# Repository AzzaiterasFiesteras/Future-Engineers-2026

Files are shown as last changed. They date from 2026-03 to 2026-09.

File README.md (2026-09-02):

<h1 align="center">Future Engineers 2026 </h1>

<table>
  <tr>
    <td>
      <p align="center">
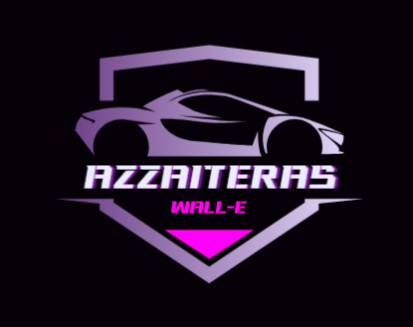
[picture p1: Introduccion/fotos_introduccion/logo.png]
Top View
      
  </tr>
</table>

 ### 📌 Table of Contents

> [!TIP]
> Click the arrow below 👇 to expand the **Table of Contents**.  
> Every item is a clickable link to a folder or README file in this repository.

<details>
<summary><b>📂 Table of Contents</b></summary>

1. [Summary README](/README.md)

2. [Introduction](/Introduccion/)  
   - [Objective](/Introduccion/Objetivo.md)
   - [Team presentation](/Introduccion/Presentacion_equipo.md)
  
3. [Initial Conditions](/Condiciones_Previas/Condiciones_Previas.md)
   -  [Materials and hardware - software relation](/Condiciones_Previas/Materiales_acabado.md)
     
4. [Mechanics](/Mecánica/)
   - [Chassis](/Mecánica/Chasis.md)
   - [Steering system](/Mecánica/Direccion.md)
     
5. [Electronics](/Electrónica/)
   - [Power system](/Electrónica/Alimentacion.md)
   - [Design](/Electrónica/Diseño.md)
   - [Components](/Electrónica/Componentes.md)
     - Servomotor
     - Board
     - Shield
     - Ultrasonic sensors
     - Gyroscope
     - Motor
     - Bateries
 6. [Programme](/Programación/)
    - [Programme development](/Programación/Explicacion_programa.md)
    - [Flow charts](/Programación/Pensamiento_lógico.md)
  7. [3D Files](/Archivos_en3D/)
  9. [Analysis](/Análisis/)
     - [Detected problems](/Análisis/Problemas_detectados.md)
     - [Improvement proposals](/Análisis/Propuestas_de_mejora.md))
   10. [Final results](/Resultado/)
11. [Conclusion](/Conclusiones/)
    - Acquired knowleadge
12. [Bibliography](/Bibliografía/)
    - Arduino
    - Tinkercad
    - PixyCam
    - LucidChart
</details>

##  Team Introduction & Team Information
<table>
  <tr>
    <td align="center" width="33%">
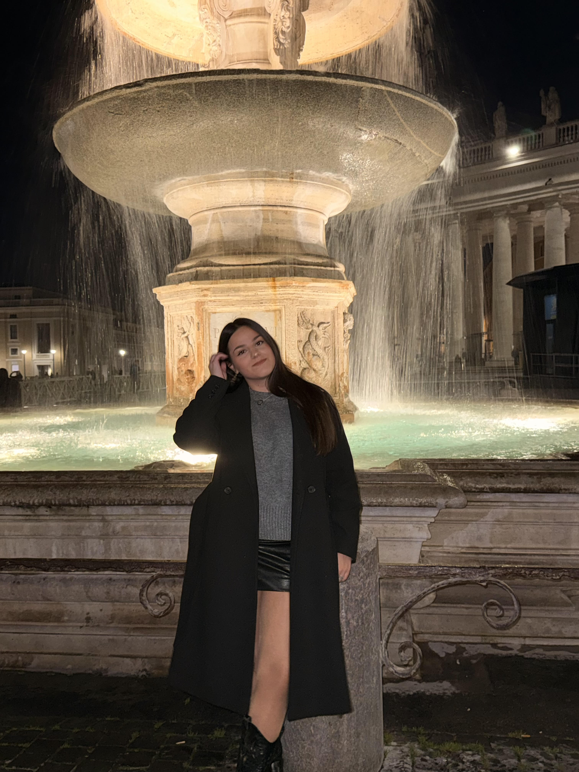
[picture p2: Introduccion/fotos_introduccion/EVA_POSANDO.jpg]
      <br>
      <strong>EVA ESPINOSA ORTIZ</strong><br>
      <em>Lead programmer</em><br>
      <sub>Sensor Integration, Logic, Obstacle Avoidance</sub>
    </td>
    <td align="center" width="33%">
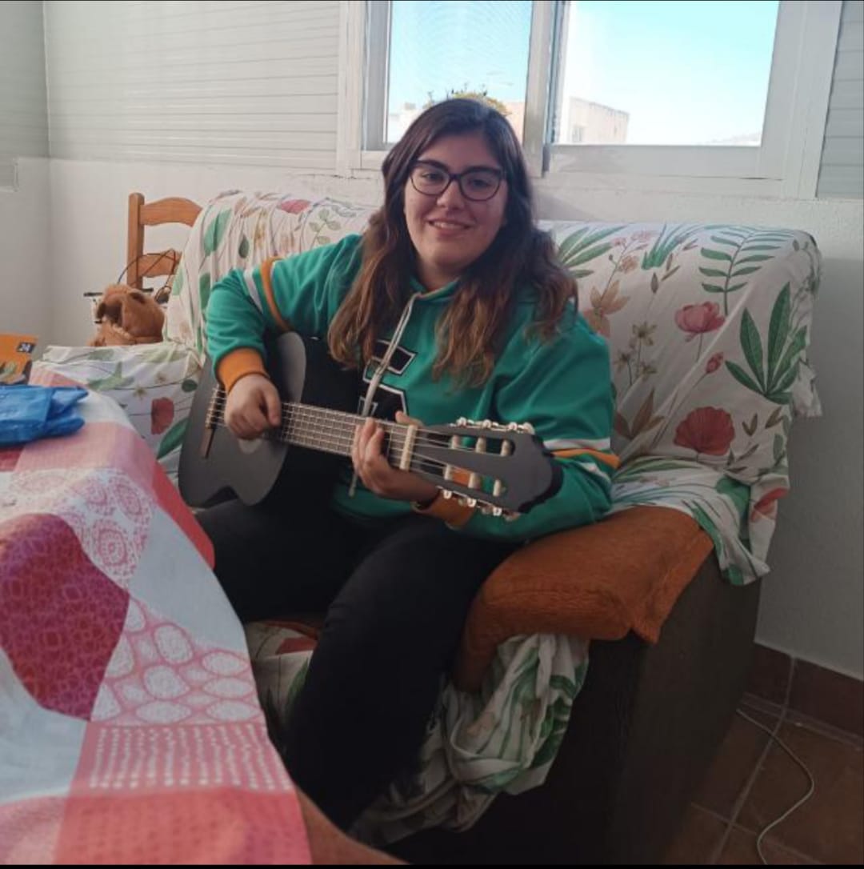
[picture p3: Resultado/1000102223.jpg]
      <br>
      <strong>LIDIA REQUENA TORRES</strong><br>
      <em>Hardware Engineer</em><br>
      <sub>Wiring, Circuit Design, Power Management</sub>
    </td>
    <td align="center" width="33%">
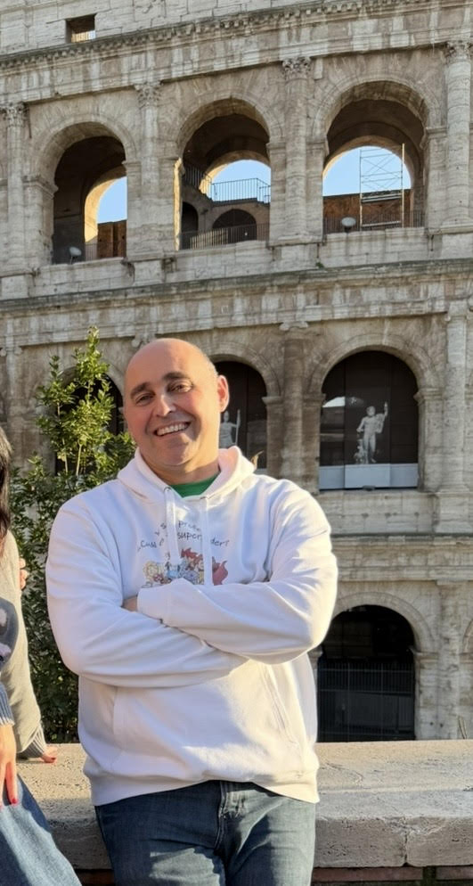
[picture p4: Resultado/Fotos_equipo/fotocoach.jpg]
      <br>
      <strong>ANTONIO MUÑOZ PANCORBO</strong><br>
      <em> Coach</em><br>
      <sub>Support and guidance </sub>
    </td>
  </tr>
</table>

---

## Introduction 
> [!WARNING]
> Click the link below 👇 to see more information about the introduction.
> 
> [For more information click here](Introduccion/)

> [!IMPORTANT]
> Click the link below 👇 to see the final result of our robot.

(https://www.youtube.com/watch?v=cXj32blsBB0)

### Presentation 
Our team´s robot is called WALLE. WALLE was designed for the Future Engineers challenge of the World Robot Olympiad. In this challenge we must complete 2 rounds. The first one, called Open Challenge, consists of completing 3 full laps around a board whose internal walls are placed randomly. The second, called Obstacle Challenge, also requires three laps on a board changing, but with the added difficulty of avoiding obstacles. Depending on the obstacles´colors (red or green) it must be avoided from the right side or the left side.
> [!WARNING]
> Click the link below 👇 to see more information.
> 
> [For more information click here](Introduccion/Objetivo.md)

### Initial Conditions
To properly carry out this project, this robot has been previously designed according to some specific rules and conditions. We had complete freedom to use any material, such as plastic, wood or even Lego pieces. However, we had a limitation in the robot´s size. The robot can not exceed 30cm x 30cm. We adapted its design in all these conditions, with special care in the front steering gear, since it was not allow to make turns with the independent motors´control as they had to be conected in the same pin. This force us to design a front steering gear with a servomotor.
> [!WARNING]
> Click the link below 👇 to see more information.
> 
> [For more information click here](Condiciones_Previas/Condiciones_Previas.md)

## Materials and hardware - software relation
1. `3D printed chassis and pins`: allows the placement of all the components with the enough space for the front steering gear not to interference with the rest of the components.
2. `Arduino Uno board`: controls all the robot´s components, such as the motors, the servomotor or the sensors. These are connected to the Arduino board
3. `MG996R servo motor`:  main responsible for the front steering gear. This is controlled by a servos library in the Arduino Ide program.
4. `TT model motor with 1:40 speed reduction`: provide robot movement. These are connected to the L298N motor driver shield for control.
5. `Wheels with a diameter of [cm]`: connected to the rear motors for their control.
6. `Three HC-SR04 ultrasonic sensors for measuring distances`: must measure and calculate the distance between the walls and the obstacles.
7. `Electronic wiring: breadboard, male-to-male jumper wires, female-to-male jumper wires, and L298N shield for motor control`: wires, protoboard and motor driver shield. Allows the comunication between the Arduino board and the rest of the components.
 8.   `Power supply`: two 3.7V 9900mAh 18650 batteries connected in series within their battery holder that provide enough energy for the correct running of the robot.
10.` BNO055 gyroscope`: allows the robot to make turns much more precisely by setting itself to specific degrees at the program.
11. `Front wheel mechanism`: made by 3D printed pieces that hold the mechanism for the robot to make turns correctly.
> [!WARNING]
> Click the link below 👇 to see more information.
> 
> [For more information click here](Condiciones_Previas/Materiales_acabado.md)

## Mechanics 
### Chassis 
For the chassis design, we opted for a smaller one than in previous years to facilitate turns on the board We also addressed the lack of space for all the components by adding an upper level where we would place the circuit board, breadboard, shield, and later, the camera. However, we also had to adjust the design to accommodate a single rear motor for the robot's drive. Therefore, we drilled two holes in the lower level of the chassis (where the ultrasonic sensors, servo motor, and front wheel mechanism are located) for the wheels. We also maintained the front wheel design from previous years. We created a small protrusion to house the servo motor and all the necessary steering mechanism components. One of the three ultrasonic sensors, in this case, the center one, would also be located on this same protrusion.

> This forms the base of the robot, upon which the other platforms will be stacked using a series of pins screwed to the structure. These plates will be secured with screws and will serve as a support for the installation of the remaining necessary components.

> [!WARNING]
> Click the link below 👇 to see more information.
>  
> [For more information click here](Mecánica/Chasis.md)

### Steering system
The steering system created is composed by an amount of components designed in 3D which act as a support and it allows you to control the trajectory you decide to make, through turns, with the servo motor and the steering system. The steering system consists of two bars which are attached to articulated joints. The bar below is the guideline that is part of the servomotor shaft. This bar is connected to the bar below through an articulated joint, as aformentioned. When the bar from above move, it allows the steering system to guide the wheels. 
> [!WARNING]
> Click the link below 👇 to see more information.
> 
>[For more information click here](Mecánica/Direccion.md)

## Electronics
### Power system
One of the the major problems was being able to prove the necessary energy to all the components. o solve this, we used two rechargeable 18650 batteries of 9900 mAh each, connected in series to a battery holder. Other options, such as AAA batteries in series, 9V batteries, or even rechargeable 9V batteries of 1300 mAh, were not efficient enough and caused voltage drops.
> [!WARNING]
> Click the link below 👇 to see more information.
> 
> [For more information click here](Electrónica/Alimentacion.md)

## Components

| Quantity | Status | Description |
| ---| --- | ---|
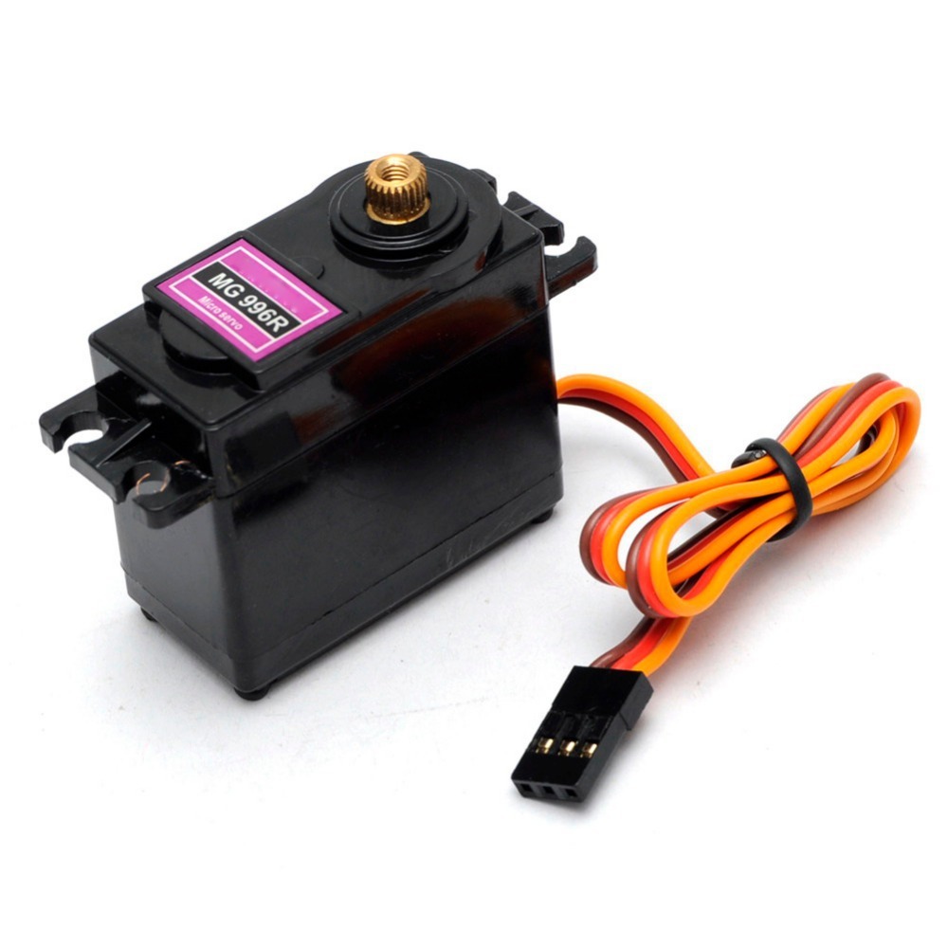
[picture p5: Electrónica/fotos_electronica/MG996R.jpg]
Servomotor MG996R
| 1 | Servomotor |  |
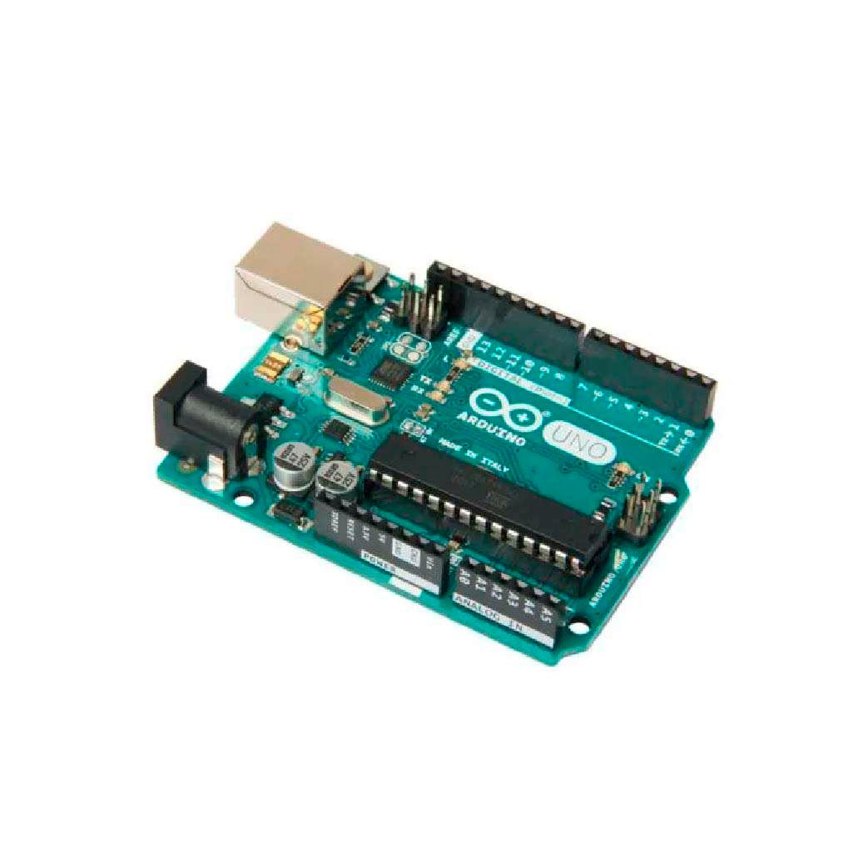
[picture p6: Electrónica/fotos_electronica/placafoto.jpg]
Arduino Uno R3 Board
| 1 | Board |  |
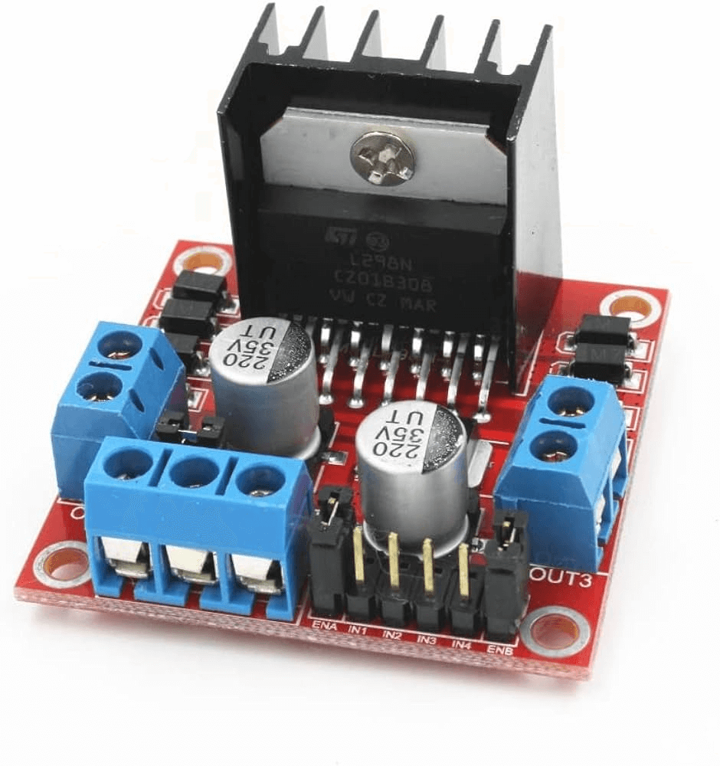
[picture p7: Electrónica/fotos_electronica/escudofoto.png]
Shield
| 1 |Shield |  |
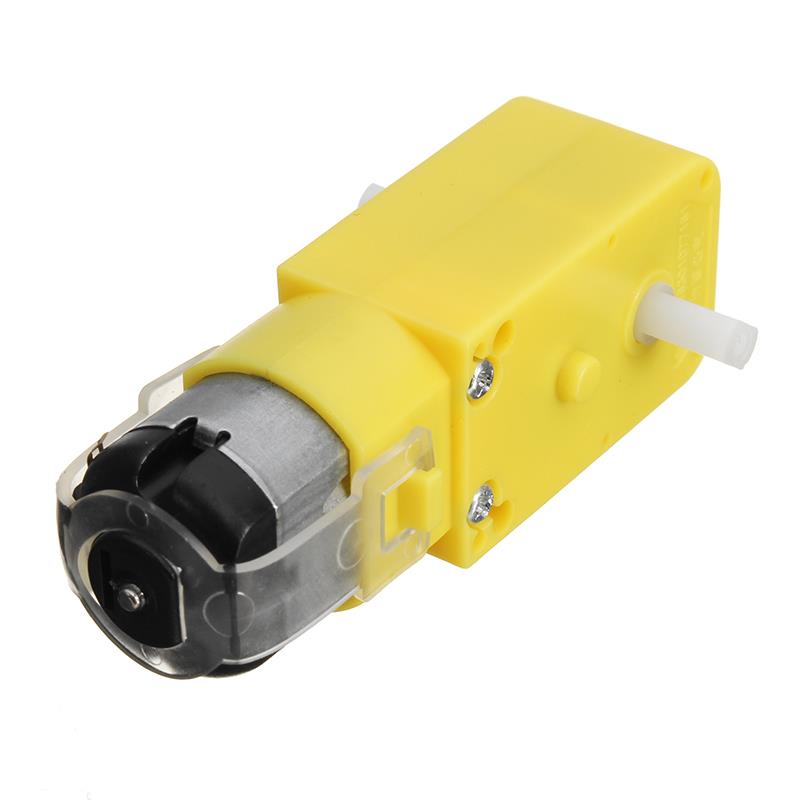
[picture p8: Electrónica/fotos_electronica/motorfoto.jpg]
Motor
| 1 |Motor|  |
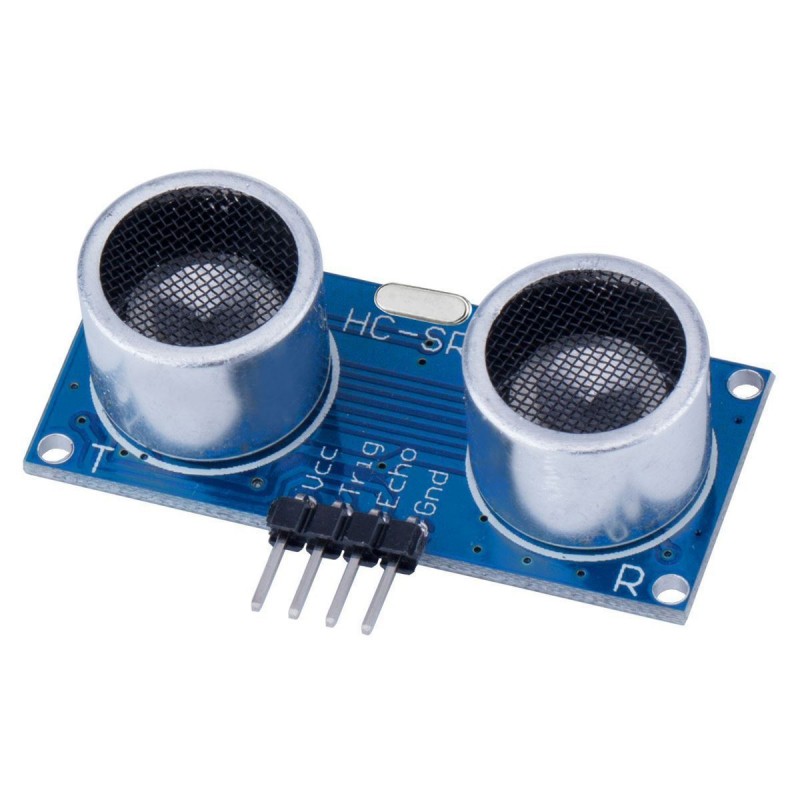
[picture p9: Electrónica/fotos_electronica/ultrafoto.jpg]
Ultrasonic sensor
| 3 | Ultrasonic sensors|  |
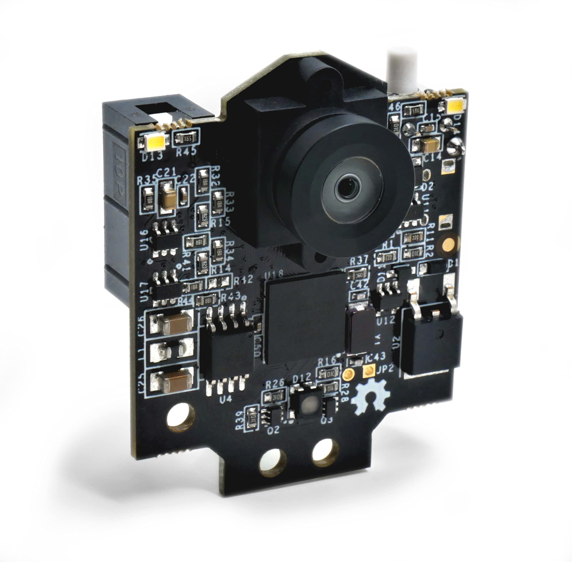
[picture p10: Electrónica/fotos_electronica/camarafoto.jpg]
Camera PixyMon 2
| 1 | Camera PixyMon 2 |  |
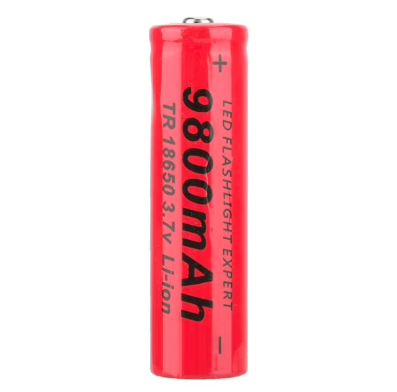
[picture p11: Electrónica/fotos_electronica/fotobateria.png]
Batteries
| 2 | Batteries |  |
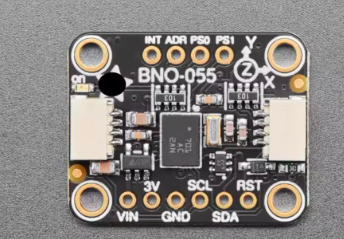
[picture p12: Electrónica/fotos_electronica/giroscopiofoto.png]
Gyroscope
| 1 | Gyroscope  |  |

### Servo Motor
For the front steering wheel was necessary the incorporation of a servo motor. We chose one that could make turns according to the turning angles to make it easier for us to program.

### Motors 
In order to WALLE to move, we used only two motors, which were installed in the back of our vehicle. To connect the motors, we used the L298N motor driver shield, which was used only as an output for controlling the motors.

### Motor driver shield
For the motor connections, we chose the L298N shield, because the previous shields were incompatible with the board. All we did was connect the shield's ena pin to pin 7 of the Arduino board to control the speed, and the motors to the in1 and in2 pins to turn them on and off.

### Sensors
To prevent the robot from crashing with walls, we used ultrasonic distance sensors. We also added a structure into the robot to hold the sensors. To program these, we created a distance measurer that allowed us to see the distance each sensor was measuring in real time on the serial monitor.

### Arduino board
We took the Arduino Uno board as we were already familiar with it. 

### Bateries
We used the 18650 batteries for our robot. Their maximum voltage is 4.2V, and the battery capacity is 9900mAh. These batteries are also rechargeable. We chose these over others due to the large number of components we had to power.

### Camera
In order to prevent the robot from crashing against obstacles, we used a PixyCam 2 Camera. This enables WALL-E to detect the color of the obstacle and decide which direction to turn (left if it is green or right if it is red).

### Gyroscope 
This component is mainly used to mesure the orientation and rotation of an object. It detects changes in angle of our robot. Henceforth, we decided to use it for its turns and for controlling the trajectory on the straight sections. We used the BNO055 gyroscope.

> [!WARNING]
> Click the link below 👇 to see more information.
> 
> [For more information click here](Electrónica/Componentes.md)

## Programme
### Open Challenge
``` c++
#include <Wire.h>
#include <Adafruit_Sensor.h>
#include <Adafruit_BNO055.h>
#include <Servo.h>
#include <Ultrasonic.h>

int ENA = 5;
int IN1 = 6;
int IN2 = 7;

Servo cochino;
Adafruit_BNO055 bno = Adafruit_BNO055(55);

const int pinservo = 9;
const int pinPulsador=13;

float anguloObjetivo;  
int centroServo = 35;  // Posición recta
int sentido = 0;       // 1 para derecha, 2 para izquierda
int contadorGiros = 0; // Control de esquinas para las 3 vueltas
int contador1=0;
int contador2=0;
bool start = false; 
```
Before developing the program logic, the first step was to install all the necessary libraries for controlling the different components of the robot, including the motors, the servo motor, the ultrasonic sensors, and the gyroscope, using #include <library_name>. The servo and the gyroscope were also declared and named, while the ultrasonic sensors were defined later in the code.

After that, all the main variables of the system were defined. The motor driver L298N pins were set (int ENA = 5, int IN1 = 6, int IN2 = 7) to control motor speed and direction. The servo motor pin was assigned (const int pinservo = 9). The variable float anguloObjetivo represents the target angle the robot must reach. int centroServo = 35 defines the position where the steering system is completely straight.

> In addition, int sentido = 0 is used to determine the initial turning direction (1 for right, 2 for left), starting at 0 until it is defined during execution. int contadorGiros = 0 is used to count the corners so the robot can stop after completing 3 laps (12 turns). The variables contador1 and contador2 are used to manage sensor-based detection conditions. Finally, bool start = false is a boolean variable that can only be true or false, initialized as false to keep the system off until it is activated by the push button.
``` C++
#define TRIG_IZQ 8
#define ECHO_IZQ 10
Ultrasonic ultraIZQ(TRIG_IZQ, ECHO_IZQ, 60000);
#define TRIG_CENTRO 3
#define ECHO_CENTRO 4
Ultrasonic ultraCENTRO(TRIG_CENTRO, ECHO_CENTRO, 60000);
#define TRIG_DERECH 11
#define ECHO_DERECH 12
Ultrasonic ultraDERECH(TRIG_DERECH, ECHO_DERECH, 60000);
```
> As we already know, ultrasonic sensors are made up of a trigger pin (which sends out a signal) and an echo pin (which receives the reflected signal). By measuring the time it takes for the signal to bounce back, we can calculate the distance to an object.
> To implement this in the program, we had to define which Arduino pins were connected to each trigger and echo pin of every sensor. The configuration was set as follows:
- Trigger (pin 8) and echo (pin 10) = left ultrasonic sensor
- Trigger (pin 3) and echo (pin 4) = center ultrasonic sensor
- Trigger (pin 11) and echo (pin 12) = right ultrasonic sensor
### Void setup
```C++
void setup() {
  Serial.begin(9600);
  pinMode(IN1, OUTPUT);
  pinMode(IN2, OUTPUT);
  pinMode(ENA, OUTPUT);
  pinMode(pinPulsador, INPUT_PULLUP);

  cochino.attach(pinservo);
  cochino.write(centroServo);
  
  Serial.println("Hola, iniciando sistema...");

  if (!bno.begin()) {
    Serial.println("No se encuentra el sensor BNO");
    while (1); // Bloqueo si no hay sensor
  }
  prepararSensor(); 
}
```
> The void setup() function is created at the beginning of the program and is executed only once when the system starts. Its main purpose is to initialize all the components required for the robot to operate correctly.
In our case, the serial port is activated to allow monitoring and calibration of sensor readings through the Serial Monitor. The servo motor pin is also configured so the steering system can start working from the beginning. In addition, the motors and the push button are initialized.A conditional statement is included to check whether the gyroscope is detected. If the BNO055 sensor is not found, an error message is printed in the serial monitor and the system is blocked to prevent further execution.
Finally, the gyroscope calibration function is called so the robot can determine its initial reference direction, often referred to as “north.”

### Void loop 
``` C++
 if (digitalRead(pinPulsador) == LOW) {
    start = true;
    Serial.print(2);
  }
  if (start == true) {
  // Lógica de fin de carrera: tras 12 giros (3 vueltas), el robot para
    if (contadorGiros >= 12) {
      terminarCarrera();
      while(1); 
    }
    int cmCentro = ultraCENTRO.Ranging(CM);
    float anguloAhora = obtenerGrados();
    int cmIzq = ultraIZQ.Ranging(CM);
    int cmDer = ultraDERECH.Ranging(CM);
```
> In the first part of the void loop, we programmed the push button so that when it is pressed, the whole program starts running. At the same time, it prints the number “2” in the Serial Monitor to verify that the button is working correctly. We also added the final race logic: after 12 turns (which equals three complete laps), the robot stops. After this, the program reads the sensor data and stores it in variables for later use. First, it measures the distances from the three ultrasonic sensors, meaning each sensor returns a value in centimeters. Then, the variable anguloAhora stores the result of the obtenerGrados() function, which returns the robot’s current orientation angle. This value is stored as a float because it can include decimal values.
``` C++
  if (cmCentro < 80) {
      contador1++;
    } else {
      contador1=0;
    }
    if (cmCentro < 140 && abs(cmIzq-cmDer)>120) {
      contador2++;
    } else {
      contador2=0;
    }
if (contador1>2 || contador2>2) {
      contador1=0;
      contador2=0;
      digitalWrite(IN1, LOW);
      digitalWrite(IN2, LOW);
      analogWrite(ENA, 0);
      delay(500);
```
> In these functions, the program uses two counters to detect when the robot needs to turn. First, the robot continuously checks the distances measured by its sensors. If it detects that it is getting too close to walls several times in a row, or if it detects an unusual situation where there is a large difference between the left and right sensor readings, it starts increasing these counters. These counters are used to make sure the situation is not just a random or temporary reading, but something that persists over time. In other words, it is a way to confirm that the sensor data is reliable. Basically, the robot does not react to a single measurement. Instead, it waits until the problem is repeated several times, and only then it responds by stopping to avoid crashing or continuing in an unsafe situation.
```C++
     if (contadorGiros == 0) {
        if (cmIzq < cmDer) sentido = 1; 
        else sentido = 2;              
        Serial.print("Sentido del circuito: ");
        Serial.println(sentido);
      }
      if (sentido == 1) hacerGiro(90);
      else hacerGiro(-90);

      contadorGiros++; 
      Serial.print("Esquina número: ");
      Serial.println(contadorGiros);
    }
```
>  It is at this point, when the robot reaches the first wall, that it decides whether the circuit will be followed on the left or on the right side. To do this, the program compares the distances measured on both sides. If the left distance is smaller than the right one, the variable sentido is set to 1, which corresponds to turning right. Otherwise, sentido is set to 2, which corresponds to turning left. Based on this decision, the robot executes the turn: if sentido is 1, it performs a 90-degree turn to the right, and if it is 2, it performs a -90-degree turn to the left.
At the same time, each turn is counted using a counter, since this value will later be used to stop the robot after completing the required number of laps. To verify that the system is working correctly, the current number of corners (and therefore turns) is displayed in the Serial Monitor.

```C++
else {
      digitalWrite(IN1, LOW);
      digitalWrite(IN2, HIGH);
      analogWrite(ENA, 200);

      // Ajuste de dirección para ir siempre rectos
      float diferencia = anguloObjetivo - anguloAhora;
      if (diferencia > 180) diferencia -= 360;
      if (diferencia < -180) diferencia += 360;

      // Si nos desviamos, el servo corrige automáticamente
      if (diferencia > 3) {
        cochino.write(centroServo + 12);
      } else if (diferencia < -3) {
        cochino.write(centroServo - 12);
      } else {
        cochino.write(centroServo);
      }
    } 
  }
}
```
> However, if the robot does not detect any walls, it means that the path is clear. In this case, the motors are activated and the speed is increased. At the same time, the direction is continuously adjusted to ensure the robot moves in a straight line. If the robot deviates from the correct path, the servo automatically corrects the steering to bring it back to a straight trajectory.

### Obstacle Challenge

## Code functions
| Function | Type | What does it do? | Use in the program |
| --- | --- | --- | --- |
| **`setup()`** | `void` | Initializes the entire robot system | Configures pins, starts serial communication, connects the servo, initializes the BNO055 sensor, and calibrates the gyroscope before starting |
| **`loop()`** | `void` | Continuously runs the robot’s main logic | Reads sensors, detects obstacles, controls movement, corrects direction, performs turns, and counts laps |
| **`obtenerGrados()`** | `float` | Gets the robot’s current angle | Reads the orientation from the BNO055 sensor and returns the current heading angle |
| **`prepararSensor()`**  | `void` | Calibrates the gyroscope | Waits until the sensor reaches maximum precision and stores the robot’s initial direction |
| **`hacerGiro()`** | `void` | Performs a controlled turn | Uses the servo and gyroscope to rotate the robot accurately |
| **`terminarCarrera()`** | `void` | Ends the race | Moves the robot forward for a few more seconds, stops the motor, and finishes execution |
| **`Serial.begin()`** | `void` | Starts serial communication | Allows messages to be sent to the Serial Monitor |
| **`Serial.print()`** | `void` | Prints information without a newline | Used for debugging and status messages |
| **`Serial.println()`**  | `void` | Prints information with a newline | Makes messages easier to read in the Serial Monitor |
| **`pinMode()`** | `void` | Configures a pin | Defines whether a pin is used as input or output |
| **`digitalWrite()`** | `void` | Turns a digital pin on or off | Controls motor direction and other devices |
| **`digitalRead()`** | `int` | Reads a digital pin | Detects whether the push button is pressed |
| **`analogWrite()`** | `void` | Sends a PWM signal | Controls motor speed |
| **`delay()`** | `void` | Pauses the program | Waits before continuing execution |
| **`abs()`** | `int / float` | Returns the absolute value | Used to calculate unsigned differences |
| **`attach()`** | `void` | Connects the servo | Enables Arduino to control the servo |
| **`write()`** | `void` | Moves the servo | Changes the steering direction |
| **`begin()`** | `bool` | Initializes the BNO055 sensor | Checks whether the sensor is working correctly |
| **`getEvent()`** | `void` | Retrieves sensor data | Reads orientation and motion data |
| **`getCalibration()`**  | `void` | Checks calibration level | Verifies gyroscope precision |
| **`Ranging()`** | `int` | Measures distance | Returns the distance detected by the ultrasonic sensor 

> [!WARNING]
> Click the link below 👇 to see more information.
> 
> [For more information click here](Programación/Explicacion_programa.md)                                                                                   |

## Compilation process
For programming, we use the Arduino IDE program. Once the program is complete, all we have to do is upload it to the board. The process of uploading the board is very simple; we just connect the board to the computer using a wire and download the program. This way, the robot is ready to work.

## Final results 
> [!WARNING]
> For seeing all the final products and our final result in the Open challenge, click the link below 👇 for seeing all the information with details.
> 
> [For more information click here](Resultado/Resultado_final.md)

## Conclusion and Analysis

> [!WARNING]
> For more information about all the acquired knowleadge and detected problems, click the link below  👇 for seeing all the information with details.
> 
> [For more information about detected problems click here](Análisis/Problemas_detectados.md)
> 
> [For more information about improvement proposals click here](Análisis/Propuestas_de_mejora.md)
> 
> [For more information about the conclusion and the acquired knowleadge click here](Conclusiones/Conocimientos_adquiridos.md)

## Bibliography 

<p align="left"> <a href="https://www.arduino.cc/" target="_blank" rel="noreferrer"> arduino </a> <a href="https://www.w3schools.com/cpp/" target="_blank" rel="noreferrer"> cplusplus </a> <a href="https://git-scm.com/" target="_blank" rel="noreferrer"> git </a> </p>

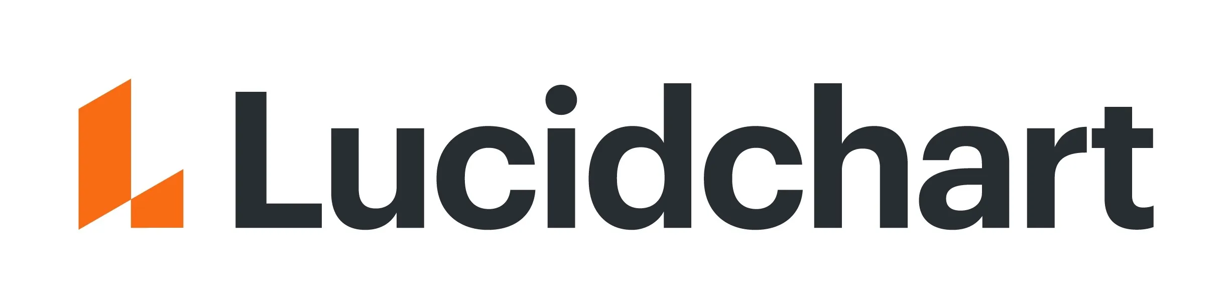
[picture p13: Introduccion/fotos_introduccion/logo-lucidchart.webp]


<p align="right">
  <a href="#top">
    
  </a>
</p>

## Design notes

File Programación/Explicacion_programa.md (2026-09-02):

# Funciones del código 

| **Funciones** |  **Sintaxis** | **Uso explicado** | 
| :--- | :---: | ---:|
| `setup()`|`void setup()`  |Se ejecuta una sola vez al encender la placa. Inicializa comunicación del puerto serie, configura pines, conecta el servo, inicia el sensor BNO055 y calibra el giroscopio| 
| `loop()`|`void loop()`  |Se ejecuta continuamente. Lee sensores ultrasónicos, detecta obstáculos, controla el movimiento, corrige dirección y cuenta los giros para completar las vueltas.| 
| `obtenerGrados()`|`float obtenerGrados() ` |Lee la orientación del sensor BNO055 y devuelve el ángulo en grados respecto al eje X `(orientation.x)`. Se usa para saber hacia dónde apunta el robot.| 
| `prepararSensor()`|`void prepararSensor() ` |Espera hasta que el giroscopio tenga máxima precisión `(gyro == 3)`. Después guarda el ángulo inicial como referencia en `anguloObjetivo.`| 
| `hacerGiro()`|`void hacerGiro(int grados) ` |Ajusta el objetivo angular y mueve el servo para girar el coche. El robot sigue girando hasta que el error sea menor a 5°.| 
| `terminarCarrera()`|`void terminarCarrera() ` |Hace que el coche avance un poco más para no seguir girando 8para que no llegue a chocarse con la pared interna) y luego apaga el motor.| 

## Funciones dentro del `void setup`

| **Funciones** | **Uso explicado** | 
| :--- | ---: |
| `Serial.begin(9600)`| Inicia comunicación del puerto serie. |
| `pinMode()`| Configura pines como entrada o salida |
| `cochino.attach(pinservo)`| Conecta el servo |
| `cochino.write(centroServo)`|`Coloca el servo centrado ` |
| `bno.begin()`|Inicializa el sensor BNO055 |
| `prepararSensor()`|Calibra el giroscopio |

## Funciones de librerías

| **Función** |**Librería** | **Uso explicado** | 
| :--- | :---: | ---:|
| `Serial.begin()`|Arduino  |Comunicación con el puerto serie| 
| `Serial.print()`|Arduino  |Mostrar texto en el puerto serie.| 
| `Serial.println()`|Arduino |Mostrar texto con salto en el puerto serie.| 
| `pinMode()`| Arduino|Configura pines| 
| `digitalWrite()`|Arduino |Encender/apagar pin.| 
| `digitalRead()` |Arduino |Leer pin digital.| 
| `analogWrite()`|Arduino  |PWM para velocidad| 
| `delay()`|Arduino  |Pausa del programa.| 
| `abs()`|Arduino/C++ |Valor absoluto.| 
| `attach()` | Servo | Conectar servo|
| `write()`  | Servo | Mover servo |
| `begin()`| BNO055 | Iniciar sensor  |

# Explicación del programa - Open Challenge
## Variables y librerías
```C++
#include <Wire.h>
#include <Adafruit_Sensor.h>
#include <Adafruit_BNO055.h>
#include <Servo.h>
#include <Ultrasonic.h>

int ENA = 5;
int IN1 = 6;
int IN2 = 7;

Servo cochino;
Adafruit_BNO055 bno = Adafruit_BNO055(55);

const int pinservo = 9;
const int pinPulsador=13;

float anguloObjetivo;  
int centroServo = 35;  // Posición recta
int sentido = 0;       // 1 para derecha, 2 para izquierda
int contadorGiros = 0; // Control de esquinas para las 3 vueltas
int contador1=0;
int contador2=0;
bool start = false; 
```
Antes de desarrollar la lógica de la programación, lo primero fue instalar las librerías tanto de los motores como del servomotor, de los sensores de ultrasonidos y del giroscopio para facilitar la programación mediante `#include <nombre de la librería>`Y además, nombrar el servo y el giroscopio. Los sensores de ultrasonidos los nombramos posteriormente. Y por último, antes de nombrar a los sensores, definimos todas las variables:
- `int ENA = 5`; `int IN1 = 6`; `int IN2 = 7`; establecemos los pines a los que van conectados los motores en el escudo L298N.
- `const int pinservo = 9;` establecemos el pin al que está conectado el servo. 
- `float anguloObjetivo:` que es el ángulo al que queremos ir.
- `int centroServo = 35; ` que es la posición del servomotor en la cual el sistema de dirección del robot está orientado para ir recto.
- `int sentido = 0; ` el robot identificará el sentido al que debe girar en el primer giro. Para esto era necesario crear una variable para la cual el valor 1 sea girar hacia la derecha y el valor 2 para la izquierda. Es por esto, que desde el principio del código establecemos que sea 0.
- `int contadorGiros = 0;` gracias a esta variable que cuenta giros, el robot es capaz de pararse al completar las 3 vueltas (12 giros en total).
- `contador1` y `contador2`: estos contadores se utilizan para asegurar que la situación no sea una lectura aleatoria o temporal, sino algo que persista en el tiempo. En otras palabras, es una forma de confirmar la fiabilidad de los datos del sensor. Básicamente, el robot no reacciona a una sola medición. En cambio, espera a que el problema se repita varias veces y solo entonces responde deteniéndose para evitar colisiones o continuar en una situación peligrosa.
- `bool start = false`: Este tipo de variable solo puede tener dos valores: true (verdadero) o false (falso). En este caso empieza en false, lo que significa que el sistema está apagado. Lo usaremos para iniciar el programa desde el pulsador.
  
```C++
#define TRIG_IZQ 8
#define ECHO_IZQ 10
Ultrasonic ultraIZQ(TRIG_IZQ, ECHO_IZQ, 60000);
#define TRIG_CENTRO 3
#define ECHO_CENTRO 4
Ultrasonic ultraCENTRO(TRIG_CENTRO, ECHO_CENTRO, 60000);
#define TRIG_DERECH 11
#define ECHO_DERECH 12
Ultrasonic ultraDERECH(TRIG_DERECH, ECHO_DERECH, 60000);
```

Como ya sabemos, los sensores de ultrasonidos están compuestos por un `trigger` (que emite una señal) y un `echo` (que recibe esa señal). Según el tiempo que tarda en rebotar esa señal podemos calcular la distancia. Para esto, tuvimos que indicar en la programación los pines a los que estaban conectados cada trigger y cada echo de cada sensor, de tal manera que:
- **Trigger** (pin 8) y **echo** (pin 10) = sensor ultrasonidos izquierda
- **Trigger** (pin 3) y **echo** (pin 4) = sensor ultrasonidos centro
- **Trigger** (pin 11) y **echo** (pin 12) = sensor ultrasonidos derecha
  
## Void setup

```C++
void setup() {
  Serial.begin(9600);
  pinMode(IN1, OUTPUT);
  pinMode(IN2, OUTPUT);
  pinMode(ENA, OUTPUT);
  pinMode(pinPulsador, INPUT_PULLUP);

  cochino.attach(pinservo);
  cochino.write(centroServo);
  
  Serial.println("Hola, iniciando sistema...");

  if (!bno.begin()) {
    Serial.println("No se encuentra el sensor BNO");
    while (1); // Bloqueo si no hay sensor
  }
  prepararSensor(); 
  
}
```
El` void setup` es una función que se crea al principio del programa y sólo se ejecuta una única vez al comienzo del programa. Su propósito principal es iniciar todos los componentes que se necesitan para comenzar a funcionar correctamente. En nuestro caso, activamos el puerto serie para poder calibrar las lecturas de los sensores de ultrasonido, y configuramos el pin del servomotor para que pueda empezar a funcionar desde el inicio. Además iniciamos los motores y el pulsador. A parte, añadimos un condicional para que en el caso de que no se detecte el giroscopio que lo imprima en el puerto serie y también bloquee el sistema. Además, llamamos a la función que calibra el giroscopio para que el robot sepa dónde está el "norte".  

## Void loop

```C++
  if (digitalRead(pinPulsador) == LOW) {
    start = true;
    Serial.print(2);
  }
  if (start == true) {
  // Lógica de fin de carrera: tras 12 giros (3 vueltas), el robot para
    if (contadorGiros >= 12) {
      terminarCarrera();
      while(1); 
    }
```
En la primera parte del void loop hemos establecido la programación del pulsador de tal manera que al pulsarlo empiece todo el programa y además, imprima en el puerto serie el número 2 para comprobar que el pulsador está funcionando. Además, añadimos la lógica del final: tras 12 giros, es decir, tres vueltas el robot se detiene. 

``` C++
    int cmCentro = ultraCENTRO.Ranging(CM);
    float anguloAhora = obtenerGrados();
    int cmIzq = ultraIZQ.Ranging(CM);
    int cmDer = ultraDERECH.Ranging(CM);
```
Aquí leemoos los datos de los sensores y los guardamos en variables para usarlos depués. Primero establecemos las distancias de los tres sensores de ultrasonidos, es decir, que lo que mida el sensor va a ser la distancia expresada en centímetros. Después, la variable anguloAhora guarda el resultado de la función obtenerGrados(). Esta función devuelve el ángulo actual del robot, y se guarda como un número decimal (`float`) porque puede tener decimales.

``` C++
  if (cmCentro < 80) {
      contador1++;
    } else {
      contador1=0;
    }
    if (cmCentro < 140 && abs(cmIzq-cmDer)>120) {
      contador2++;
    } else {
      contador2=0;
    }
if (contador1>2 || contador2>2) {
      contador1=0;
      contador2=0;
      digitalWrite(IN1, LOW);
      digitalWrite(IN2, LOW);
      analogWrite(ENA, 0);
      delay(500);
```
En estas funciones el programa está usando dos contadores para detectar cuando el robot necesitaría girar. Primero, el robot va comprobando las distancias con sus sensores. Si detecta que se acerca a las paredes varias veces seguidas, o si detecta una situación rara donde hay mucha diferencia entre lo que ve a la izquierda y a la derecha, empieza a sumar en unos contadores. Estos contadores sirven para asegurarse de que no es algo puntual, sino que realmente el problema se mantiene durante un tiempo. Es básicamente una manera de asegurar que las mediciones de los sensores son correctas. En otras palabras, el robot no reacciona a un solo dato, sino que espera a que el problema se repita varias veces, y entonces se para para evitar chocar o seguir en una mala situación.

``` C++
     if (contadorGiros == 0) {
        if (cmIzq < cmDer) sentido = 1; 
        else sentido = 2;              
        Serial.print("Sentido del circuito: ");
        Serial.println(sentido);
      }
      if (sentido == 1) hacerGiro(90);
      else hacerGiro(-90);

      contadorGiros++; 
      Serial.print("Esquina número: ");
      Serial.println(contadorGiros);
    }
```
Es entonces, cuando en la primera pared decidimos si el circuito se hace por la izquierda o por la derecha. Además, establecemos que si la distancia de la izquierda es menor que la de la derecha, entonces el sentido va a ser el 1; el correspondiente a la derecha. Y por lo tanto, si es al revés el sentido va a ser el 2; el que corresponde a la izquierda. Por lo tanto para la ejecución del giro decimos que si el sentido es el 1 (derecha) entonces que el robot haga un giro de 90 grados. Y si es al revés, que haga un giro de -90 grados para girar a la izquierda (sentido 2). Además, conforme vamos haciendo los giros los vamos contando ya que posteriormente los necesitaremos para parar el robot. Para asegurarnos de que el contador de giros está funcionando, mostramos en el puerto serie el número de esquinas, y por tanto, de giros. 

``` C++
else {
      digitalWrite(IN1, LOW);
      digitalWrite(IN2, HIGH);
      analogWrite(ENA, 200);

      // Ajuste de dirección para ir siempre rectos
      float diferencia = anguloObjetivo - anguloAhora;
      if (diferencia > 180) diferencia -= 360;
      if (diferencia < -180) diferencia += 360;

      // Si nos desviamos, el servo corrige automáticamente
      if (diferencia > 3) {
        cochino.write(centroServo + 12);
      } else if (diferencia < -3) {
        cochino.write(centroServo - 12);
      } else {
        cochino.write(centroServo);
      }
    } 
  }
}
```

Sin embargo, si el robot no detecta ninguna pared, significa que el camino está libre, por lo cual activamos los motores y aumentamos su velocidad y además ajustamos la dirección para que siempre vaya recto y por tanto si el robot se desvía, el servo se corrige automáticamente.

## Funciones propias 
``` C++
float obtenerGrados() {
  sensors_event_t datos;
  bno.getEvent(&datos);
  return datos.orientation.x;
}
```
Este código sirve para que el robot pueda saber hacia dónde está girado, calibrarse y hacer giros precisos usando un sensor BNO055 (un giroscopio). Esta lee el sensor de orientación del robot. El sensor le dice en qué dirección está mirando (como una brújula). La función guarda esos datos y devuelve el ángulo actual del robot, es decir, cuántos grados está girado.
```C++
void prepararSensor() {
  uint8_t sys, gyro, accel, mag;
  Serial.println("Esperando calibración del giroscopio...");
  do {
    bno.getCalibration(&sys, &gyro, &accel, &mag);
  } while (gyro < 3); // Nivel 3 es el máximo de precisión
  
  delay(1000);
  anguloObjetivo = obtenerGrados(); // Fijamos el rumbo inicial
  Serial.println("Sensor listo.");
}
```
Este subprograma sirve para preparar el sensor antes de empezar a usar el robot. El programa espera hasta que el giroscopio esté bien calibrado. Mientras no esté bien calibrado, el robot no hace nada. Cuando ya está listo, espera un segundo y guarda la dirección actual como anguloObjetivo, es decir, el rumbo inicial que quiere mantener o usar como referencia. Luego avisa por pantalla que el sensor ya está listo.
```C++
void hacerGiro(int grados) {
  anguloObjetivo = anguloObjetivo + grados;

  // Ajuste para no salir del rango 0-360
  if (anguloObjetivo >= 360) anguloObjetivo -= 360;
  if (anguloObjetivo < 0) anguloObjetivo += 360;

  // Movemos el servo para girar
  if (grados > 0) cochino.write(centroServo + 35);
  else cochino.write(centroServo - 35);

  digitalWrite(IN1, LOW);
  digitalWrite(IN2, HIGH);
  analogWrite(ENA, 140);
```
Este subprograma sirve para girar el robot una cantidad exacta de grados. Primero calcula el nuevo objetivo sumando los grados que quiere girar. Después ajusta ese valor para que siempre esté entre 0 y 360 grados, como si fuera un círculo. Luego el robot empieza a girar: mueve el servo para ayudar al giro (dependiendo si gira a la derecha o izquierda), activa el motor en una dirección y le da una velocidad más lenta para que el giro sea más preciso y le de tiempo a girar sin problema. 
``` C++
 float dist;
  do {
    float actual = obtenerGrados();
    dist = anguloObjetivo - actual;
    if (dist > 180) dist -= 360;
    if (dist < -180) dist += 360;
  } while (abs(dist) > 5); // El bucle para cuando el error es menor a 5 grados

  cochino.write(centroServo); // Enderezamos ruedas
  delay(200);
```
Mientras el robot está girando, entra en un bucle donde está constantemente mirando su orientación actual con el sensor. Va comparando la posición actual con la posición objetivo y calcula el error (la diferencia entre ambos ángulos). Si esa diferencia es mayor de 5 grados, sigue girando. Cuando finalmente el robot está lo suficientemente cerca del ángulo deseado (menos de 5 grados de error), se detiene el giro, endereza las ruedas y espera un pequeño tiempo para estabilizarse.

``` C++
void terminarCarrera() {
  Serial.println("¡Última vuelta completada! Cruzando meta...");
  cochino.write(centroServo);
  digitalWrite(IN1, LOW);
  digitalWrite(IN2, HIGH);
  analogWrite(ENA, 180);
  delay(2000); // Avanza 2 segundos extra para quedar bien posicionado al final
  
  analogWrite(ENA, 0); 
  digitalWrite(IN2, LOW);
  Serial.println("Carrera finalizada con éxito.");
}
```
Esta función sirve para que, cuando el robot termina la carrera, no intente girar ni corregir la dirección, sino que se mantenga completamente recto. Para eso primero centra el servo y luego hace que avance en línea recta durante unos segundos y entonces se detiene por completo. Este subprograma está pensado para asegurar que al final el robot siga recto y que no le pille el contador de giros a mitad de uno. 

# Explicación del programa - Obstacle Challenge
## Variables y librerías
```C++
#include <Wire.h>
#include <SPI.h>
#include <Adafruit_Sensor.h>
#include <Adafruit_BNO055.h>
#include <Servo.h>
#include <Ultrasonic.h>
#include <Pixy2.h>
```

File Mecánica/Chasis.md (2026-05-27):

# Diseño del chasis
Para el diseño del chasis pensamos en crear uno más pequeño que en años anteriores para así nos facilitara realizar los giros en el tablero y no hubiera que hacer demasiadas maniobras. Además, solucionamos la falta de espacio para la colocación de todos los componentes añadiendo un piso superior en donde colocaríamos la placa, la protoboard, el escudo y posteriormente la cámara. Sin embargo, también tuvimos que ajustar el diseño de tal manera que nos permitiera utilizar un solo motor trasero que sería la tracción de nuestro robot. Por esta razón, hicimos en la planta baja del chasis (donde van los sensores de ultrasonidos, el servomotor, y el mecanismo de las ruedas delanteras) dos agujeros en los que iran las ruedas. También, hemos mantenido el diseño de años pasados en lo que respecta al chasis respecto a las ruedas delanteras. Hemos hecho un pequeño saliente en donde estableceríamos el servomotor, y con este todas las piezas necesarias para el mecanismo de dirección. En ese mismo saliente, también estaría ubicado uno de los tres sensores de ultrasonidos. En este caso el del centro.

Esta constituye la base del robot, sobre la cual se irán apilando las demás plataformas mediante una serie de pasadores atornillados a la estructura. Estas placas serán fijadas con tornillos y servirán como soporte para la instalación del resto de los componentes necesarios.

<p align="center">
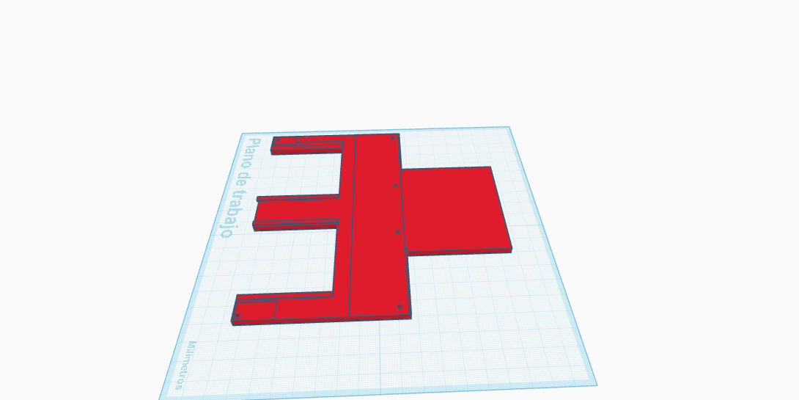
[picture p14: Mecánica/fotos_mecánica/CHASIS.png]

</p>

> [!TIP]
> Click the link below 👇 to see all 3D designs in .STL.
> 
> [For more information click here](Archivos_en3D/)

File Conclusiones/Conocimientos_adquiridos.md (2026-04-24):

# Conocimientos adquiridos 

Participar en el proyecto Future Engineers de la World Robot Olympiad ha sido una experiencia sumamente enriquecedora, en la cual hemos adquirido múltiples conocimientos en muchos ámbitos relacionados no sólo con la robótica sino también con la tecnología. A lo largo del desarrollo del proyecto, hemos aprendido y experimentado lo siguiente: 

- Electrónica básica: mediante este proyecto hemos aprendido algunos conceptos simples de la electrónica como el uso de placas como Arduino o el conexionado de todos los componenetes como el servomotor y los sensores ultrasónicos.

- Programación y robótica: hemos aprendido un lenguaje de código nuevo Arduino (C/C++) y también a incluir el control nuevos escudos en la programación y distintos componentes.

- Pensamiento crítico: la capacidad de identificar y saber resolver problemas mediante soluciones innovadoras fue crucial para este proyecto. A medida que fuimos avanzando, adquirimos mayor experiencia y confianza, lo que nos permitió detectar los problemas con mayor rapidez y eficacia. Esta evolución no solo mejoró el funcionamiento del robot, sino que también fortaleció nuestra capacidad de pensar de forma crítica 

- Energía: gracias a todas las dificultades respecto a la alimentación del robot, hemos adquirido conocimientos sobre los diferentes tipos de batería y cómo elegir la más adecuada según el consumo de energía del robot.

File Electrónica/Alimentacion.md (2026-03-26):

# Alimentación del robot

## Conexionado 
Para el conexionado de todos los componentes hemos necesitado tanto la placa de control Arduino, como una protoboard y un escudo. La placa junto a la protoboard han servido para la conexión de todos los compenentes menos los motores, los cuales hemos conectado al escudo.

### Conexionado del Escudo L298N
Lo primero fue conectar el motor al escudo. La alimentación, la consigue mediante los OUT1 y OUT2. Y para el control y la posterior programación de este; necesitamos establecer el pin IN1, IN2, y ENA. Los cuales controlan la dirección a la que gira el motor (para alante o para atrás) y la velocidad. En nuestro caso, así hemos establecido estos pines:
1. ENA: pin 5
2. IN1: pin 6
3. IN2: pin 7
<p align="center">
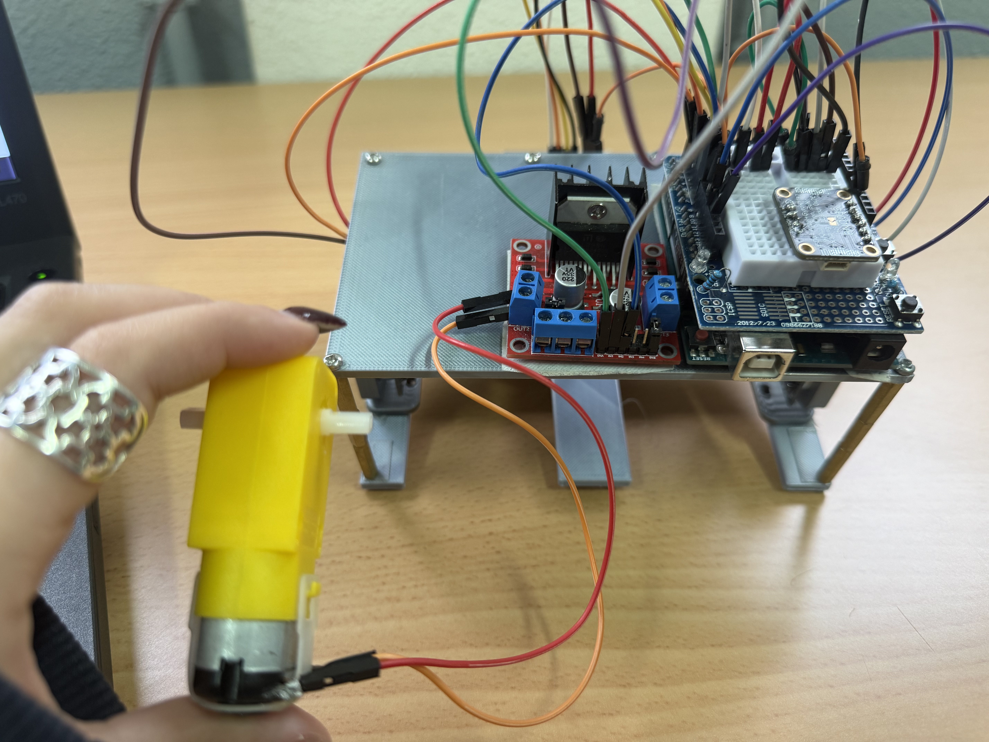
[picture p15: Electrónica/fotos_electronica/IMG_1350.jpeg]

</p>
   
### Conexionado de los sensores de ultrasonidos
Para el correcto funcionamento de nuestro robot, necesitábamos al menos 3 sensores de ultrasonidos que midieran las distancias entre las paredes. Estos sensores tienen 4 pines a los que conectarse. Uno de 5V y otro de GND los cuales le proporcionan la energía que necesita para funcionar. Y después, tiene otros dos pines más de control, el TRIGGER y el ECHO; que uno emite la señal y el otro la recibe. Así es cómo lo hemos conectado:
- Ultrasonidos de la izquierda
1. VCC: 5V
2. TRIGGER: pin 2
3. ECHO: pin 1
4. GND: GND
- Ultrasonidos del centro
1. VCC: 5V
2. TRIGGER: pin 3
3. ECHO: pin 4
4. GND: GND
- Ultrasonidos de la derecha
1. VCC: 5V
2. TRIGGER: pin 11
3. ECHO: pin 12
4. GND: GND
   
<p align="center">
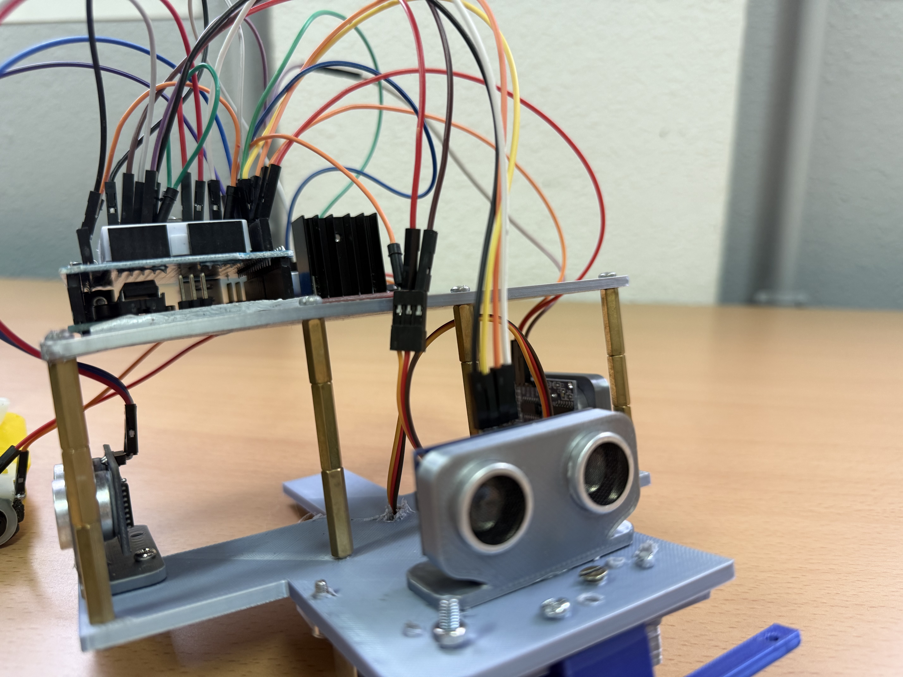
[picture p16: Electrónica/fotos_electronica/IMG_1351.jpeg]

</p>

### Conexionado del servomotor
Para los giros era necesario incorporar un mecanismo de dirección delantero. Para eso utilizamos un servomotor, el cual conectamos a 5V, a GND y al pin 9.

## Baterías
Uno de los mayores desafíos que enfrentamos durante el montaje del robot fue la implementación de su sistema de alimentación. Desde el inicio del proyecto, quedó claro que alimentar de manera eficiente todos los componentes: motores, sensores, placa y posibles componentes adicionales, no sería tarea sencilla. Algunas razones por las que tuvimos que escoger estas pilas son:

Las pilas de 9 V no ofrecían suficiente corriente para alimentar los motores sin caídas de tensión.
Las pilas más pequeñas AAA, incluso apiladas en serie, no proporcionaban la capacidad energética necesaria para mantener el robot funcionando por largos periodos.
Otra opción también era utilizar de 9 V recargables de 1300mAh. Sin embargo de experiencias anteriores ya éramos conocedores de que no serviría ya que no tiene la capacidad para alimentar a todos los componentes necesarios. 
 <p align="center">
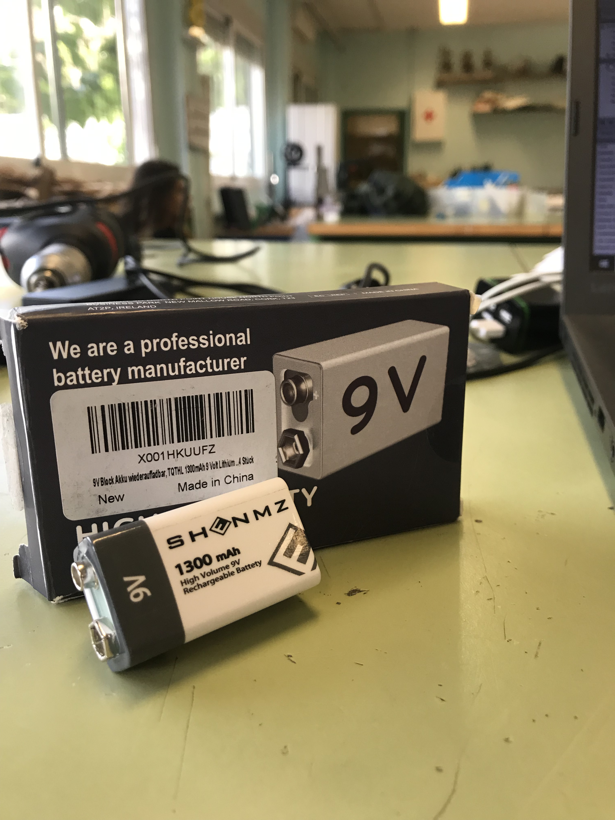
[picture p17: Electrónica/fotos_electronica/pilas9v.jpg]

</p>
 Por esto, decidimos optar por el uso de dos baterías recargables tipo 18650 de 9900 mAh cada una, conectadas en serie mediante un portapilas específico para este formato. Además de proporcionar un voltaje suficiente, también dotaba al robot de una alta capacidad de carga (autonomía prolongada).
  <p align="center">
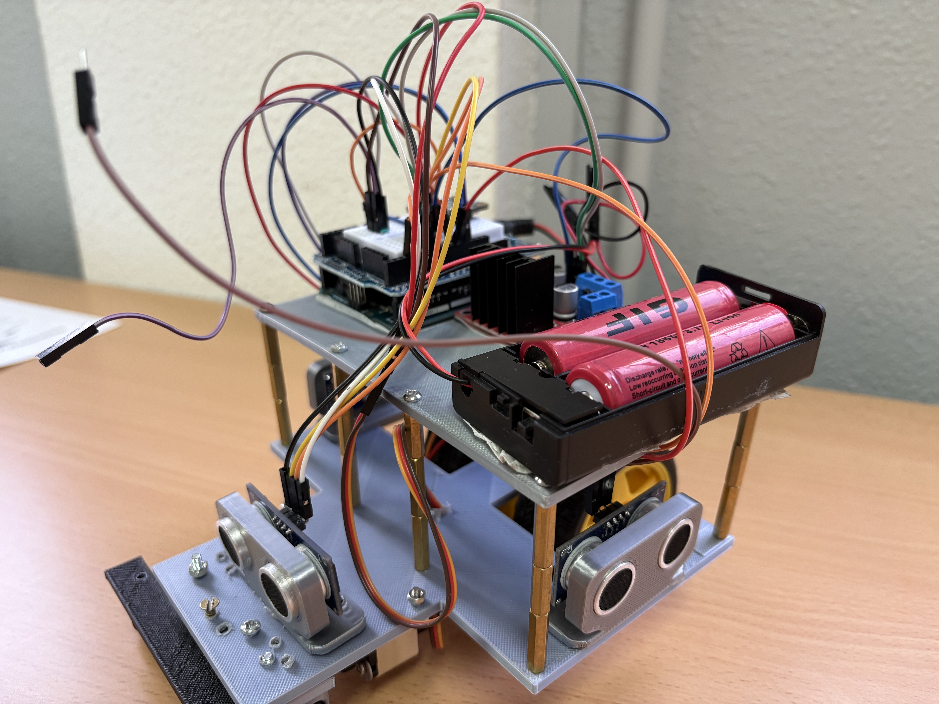
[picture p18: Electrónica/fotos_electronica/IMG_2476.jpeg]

</p>

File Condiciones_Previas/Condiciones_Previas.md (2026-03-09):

# Condiciones Previas
Tamaño limitado del robot: 30cm x 30cm
Montaje: piezas de cualquier material. Permitido Arduino y Lego.
Diseño adaptado a los componentes del robot, con especial cuidado en el mecanismo de las ruedas delanteras. 

# Reglamento 
Las condiciones previamente expuestas han sido establecidas en estricto cumplimiento con el reglamento oficial publicado por la World Robot Olympiad (WRO). Este reglamento sirve como marco normativo para regular todos los aspectos de la competición Future Engineers, garantizando así que cada participación se ajuste a los estándares establecidos. Las directrices y requisitos señalados han sido cuidadosamente elaborados para asegurar la integridad, la equidad y la transparencia en el desarrollo y evaluación de los proyectos. Se enfatiza la necesidad de que cada equipo revise y respete íntegramente las disposiciones aquí detalladas, ya que su cumplimiento resulta esencial no solo para la validación del robot, sino también para la correcta ejecución del proceso competitivo conforme a las normativas internacionales.
Normativa Future Engineers (enlace)

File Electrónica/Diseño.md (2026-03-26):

# Diseño de toda la electrónica
Para la realización del diseño de la electrónica de nuestro robot hemos utilizado el programa TinkerCad ya que nos permite ver de una manera mucho más visual y clara todo el conexionado eléctrico. 
<p align="center">
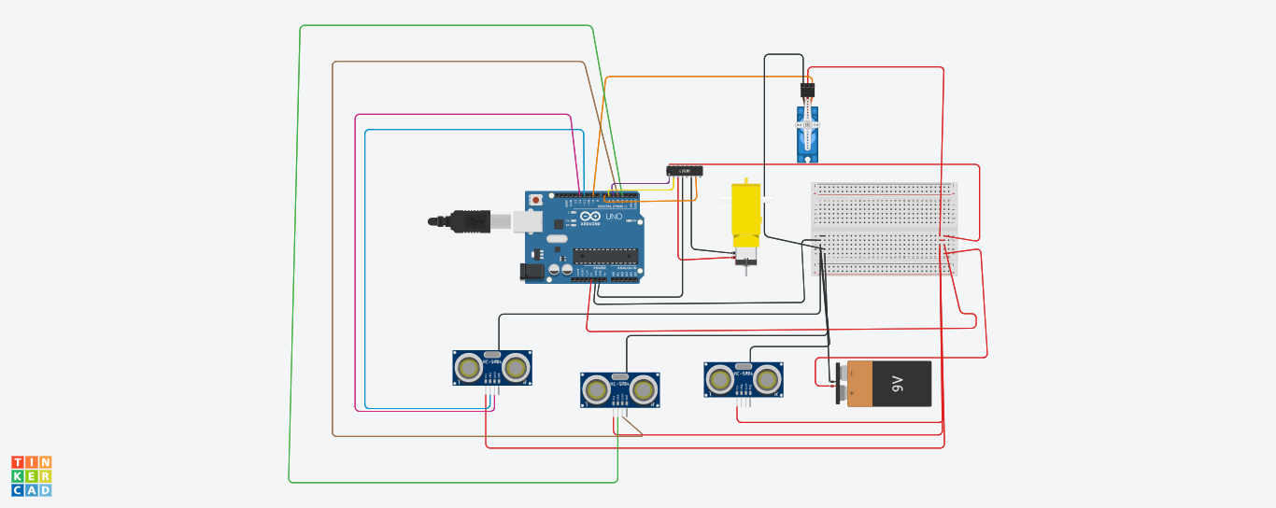
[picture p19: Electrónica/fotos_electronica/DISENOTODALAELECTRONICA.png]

</p>

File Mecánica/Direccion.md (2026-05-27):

# Mecanismo de dirección
El mecanismo de diección consiste en un conjunto de componentes del vehículo construido, que permite controlar la trayectoria que decidimos hacer, a través de giros, con el servomotor y el sistema de dirección. 

## Funcionamiento del mecanismo
En el centro del eje se encuentra un servomotor, que gira a izquierda o derecha. Ese mismo servo está unido a una barra que conecta ambas ruedas. Cada rueda está conectada a  una pieza impresa en 3D con forma cilíndrica (parecido a un “chupachups”). Esa pieza cilíndrica gira dentro de una carcasa redonda, que actúa como soporte y permite el giro suave, en la cual se produce la fuerza de rodamiento, lo que va a permitir que nuestras ruedas giren. El sistema funciona de tal manera que cuando el servomotor mueve el sistema de dirección (previamente montado) y por tanto, orienta el sentido al que queremos dirigir las dos piezas cilíndricas, es decir, las ruedas. Esto permite que el robot se desplace hacia la izquierda o la derecha según se necesite. La barra unicamente sirve como conexión y soporte de ambas ruedas y al chasis.


(https://www.youtube.com/watch?v=K2S8Ee-0UtI)

## Diseños en 3D utilizados 

- En este primer diseño, creamos la barra horizontal conectada a ambas ruedas, la cual sirve como soporte y unión de las ruedas al chasis. Esta pieza, necesitaba tener las medidas adecuadas para que pudiera encajar en el diseño y además, coincidiera con la altura ideal para las ruedas. Fue una de las más sencillas de diseñar y posteriormente imprimir.
<p align="center">
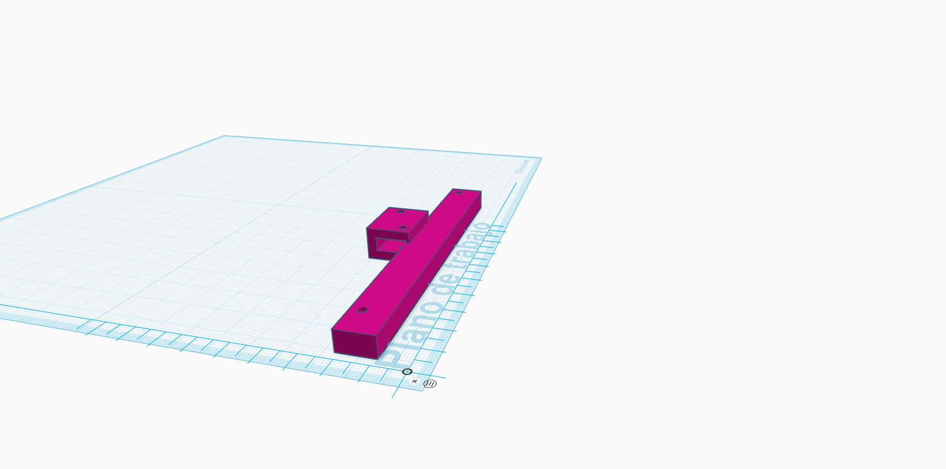
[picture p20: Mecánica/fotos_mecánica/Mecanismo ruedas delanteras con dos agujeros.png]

</p>

- En este segundo diseño, creamos la pieza cilíndrica para que gire dentro de una carcasa previamente diseñada e impresa. Esta pieza, es muy similar a un chupachups, lo cual nos va a permitir que gire sin problema en la carcasa, y por tanto, giren las ruedas. Posteriormente hemos necesitado limar un poco los bordes de la esfera para facilitar su rozamiento en la carcasa que la envuelve. Este diseño también tuvo que ser a medida para que la parte plana midiera exactamento lo mismo que el hueco de la rueda para que encajara de manera perfecta. Además, también creamos la carcasa en la que se encuentra envuelta la anterior pieza cilíndrica. Para ello tuvimos varios impedimentos y dificultades. El principal fue la dificultad del diseño 3D ya que la pieza era dificil de visualizar e idear. Una vez que ya la teniamos visualizada, con un poco de ayuda, fue relativamente fácil su realización en la interfaz de TinkerCad. La razón por la cual diseñamos esta pieza posteriormente de tener la cilíndrica, fue porque necesitabamos que esta se adaptara completamente a la cilíndrica y por tato necesitabamos tener sus medidas exactas. La carcasa cuenta con los agujeros y huecos necesarios para poder conectarlo e integrarlo fácilmente con el sistema de dirección.
<p align="center">
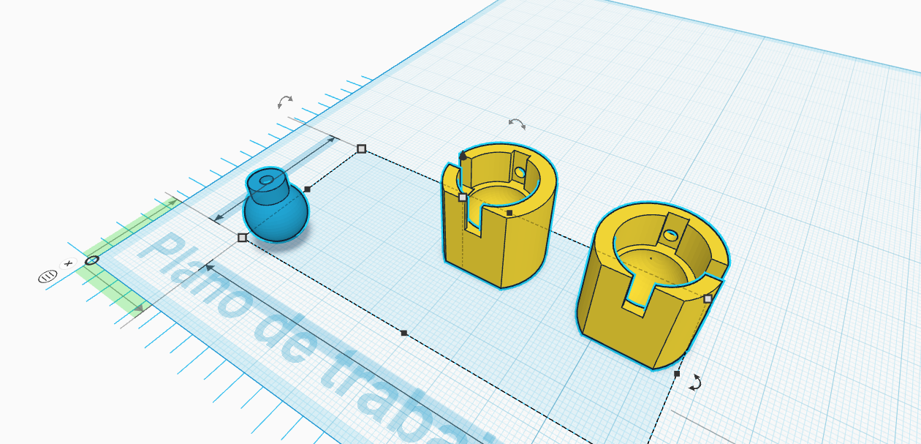
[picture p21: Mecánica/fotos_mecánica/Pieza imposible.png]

</p>

- En el último diseño para el mecanismo de dirección creamos un mero soporte para que las barras de este estuvieran en sus respectivos sitios y permitieran que estas barras metálicas se pudieran desplazar y por tanto, pudiera girar todo el mecanismo.
<p align="center">
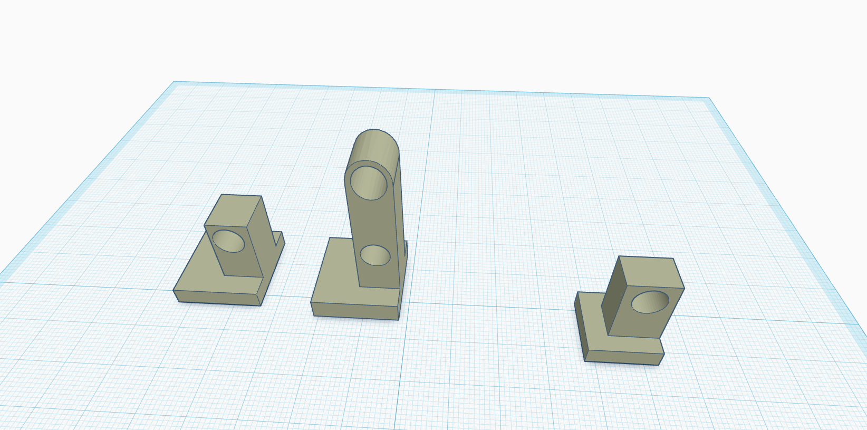
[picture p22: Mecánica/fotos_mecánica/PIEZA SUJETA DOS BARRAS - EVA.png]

</p>

Todas estas piezas han sido diseñadas en la interfaz de TinkerCad en 3D y posteriormente impresas en una impresora 3D la cual disponemos en el instituto. Asimismo, todas las piezas han sido colocadas y atornilladas en la chasis. 
> [!TIP]
> Click the link below 👇 to see all 3D designs in .STL.
> 
> [For more information click here](Archivos_en3D/)

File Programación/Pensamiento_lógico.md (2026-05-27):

# Diagramas de flujo 
## Open Challenge
<p align="center">
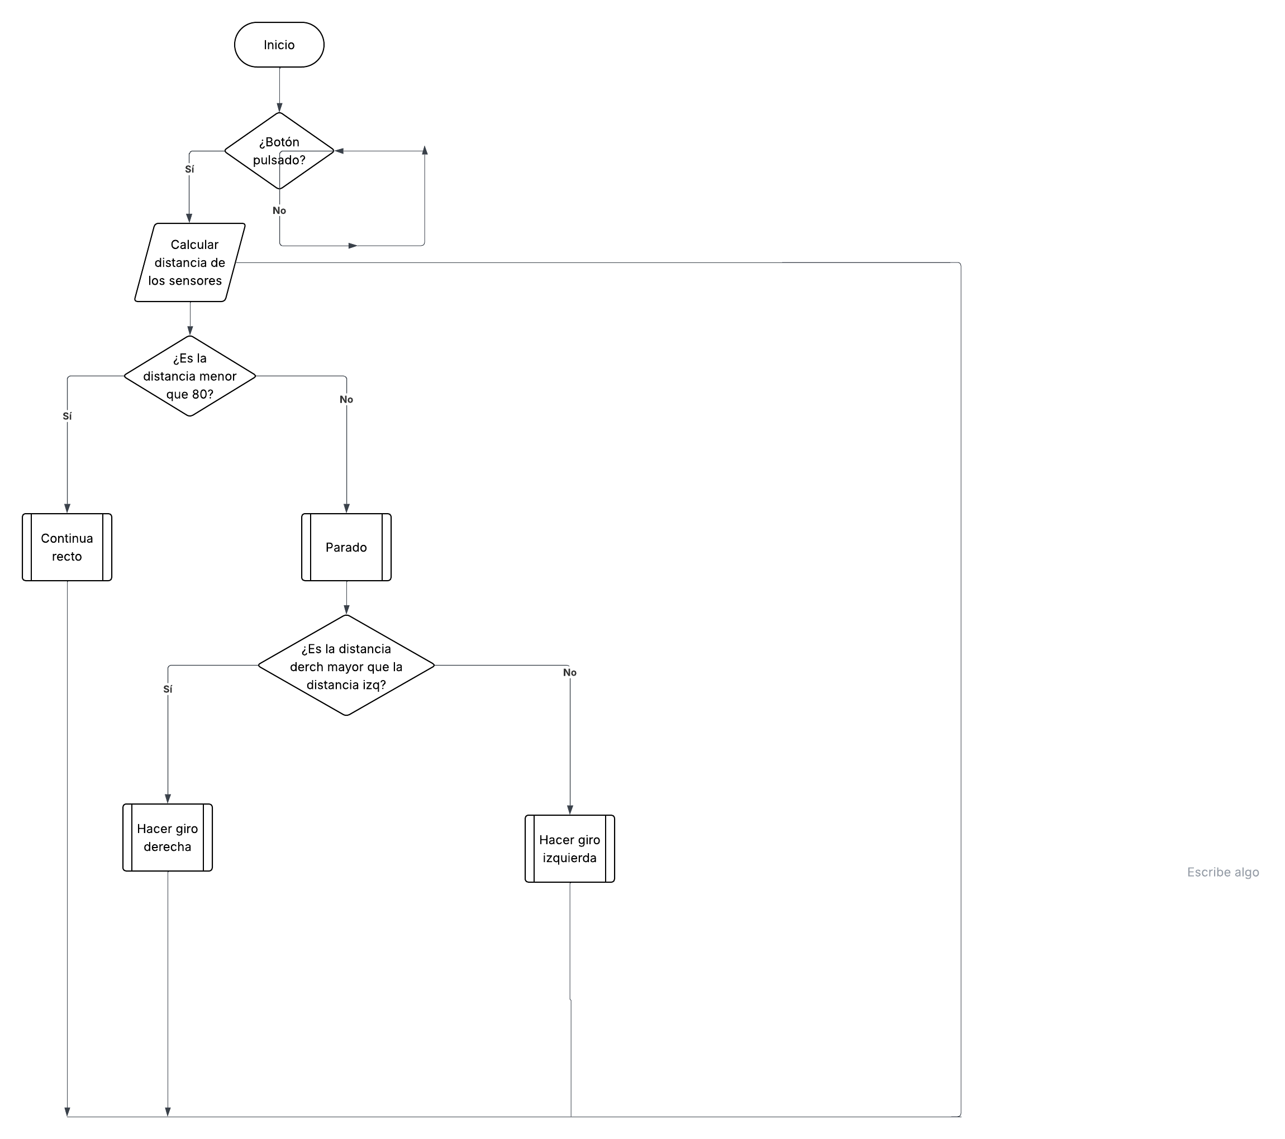
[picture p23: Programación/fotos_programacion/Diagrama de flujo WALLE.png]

</p>

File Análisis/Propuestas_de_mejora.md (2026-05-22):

# Propuestas de mejora 
Para mejorar el robot en un futuro, planteamos implementar un sistema de detección de obstáculos mediante una cámara. Actualmente, el programa para esta función ya ha sido desarrollado y puede detectar los bloques verdes y rojos mediante procesamiento de imagen. También, disponemos de imágenes que prueban dicho funcionamiento en las que se pueden ver la detección de colores .

<p align="center">
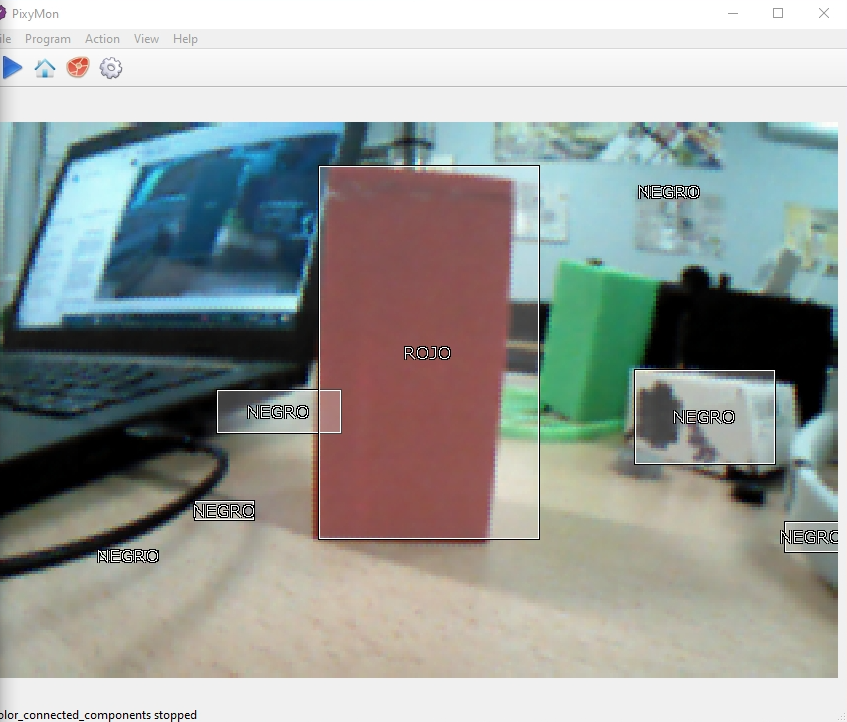
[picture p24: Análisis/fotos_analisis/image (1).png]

</p>

<p align="center">
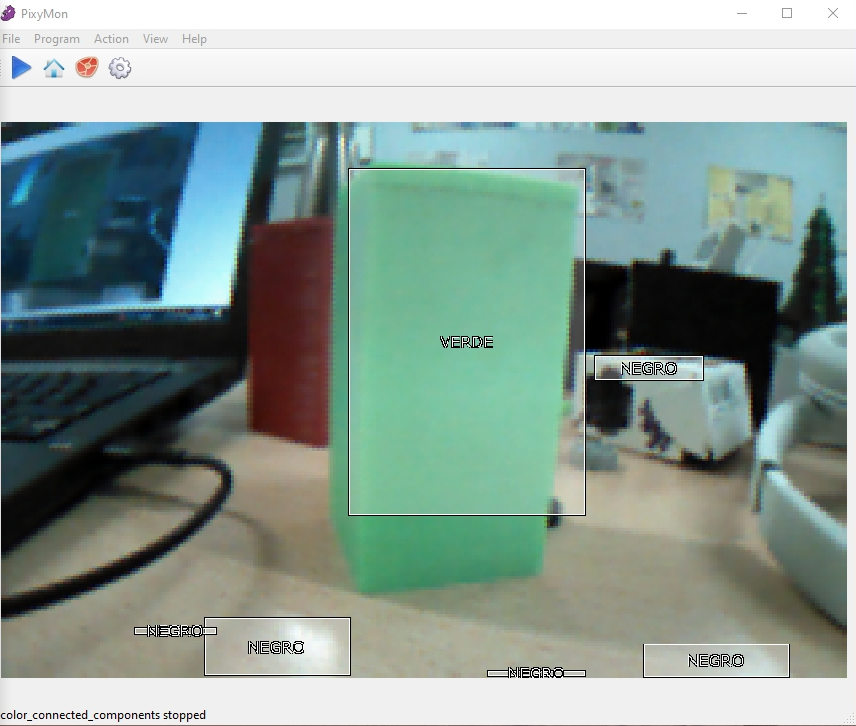
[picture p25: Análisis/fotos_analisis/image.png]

</p>

<p align="center">
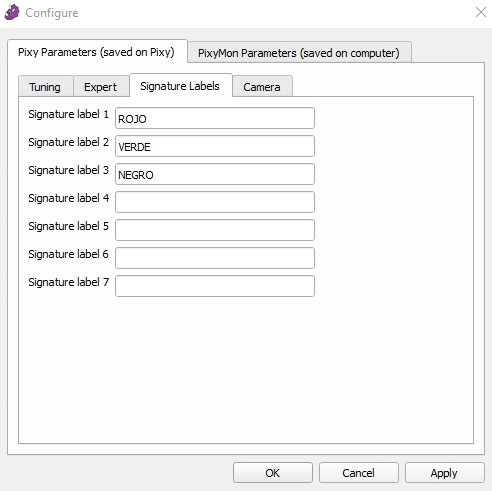
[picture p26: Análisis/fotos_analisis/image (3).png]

</p>

<p align="center">
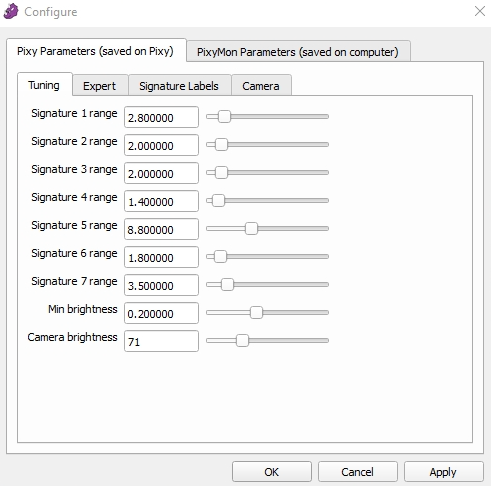
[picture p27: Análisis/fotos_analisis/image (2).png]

</p>

El programa consiste en que, una vez que se detecta el bloque de obstáculos, el robot haga un giro en función del color identificado. (si es rojo esquiva a la derecha y si es verde a la izquierda). Sin embargo, este todavía no se ha probado todavía físicamente en el robot por limitaciones de tiempo para terminar de desarrollar todo.
Por tanto, las tareas pendientes para completar esta mejora son las siguientes:

- Integración física de la cámara en el robot.
- Ajuste y calibración de los parámetros de detección de color para mejorar la precisión y estabilidad del reconocimiento.
- Realización de pruebas reales de funcionamiento y validación del comportamiento del robot ante la detección de objetos. Aunque la implementación completa no ha podido finalizarse dentro del tiempo disponible, la base del sistema ya está desarrollada y preparada para futuras mejoras y pruebas.

<p align="center">
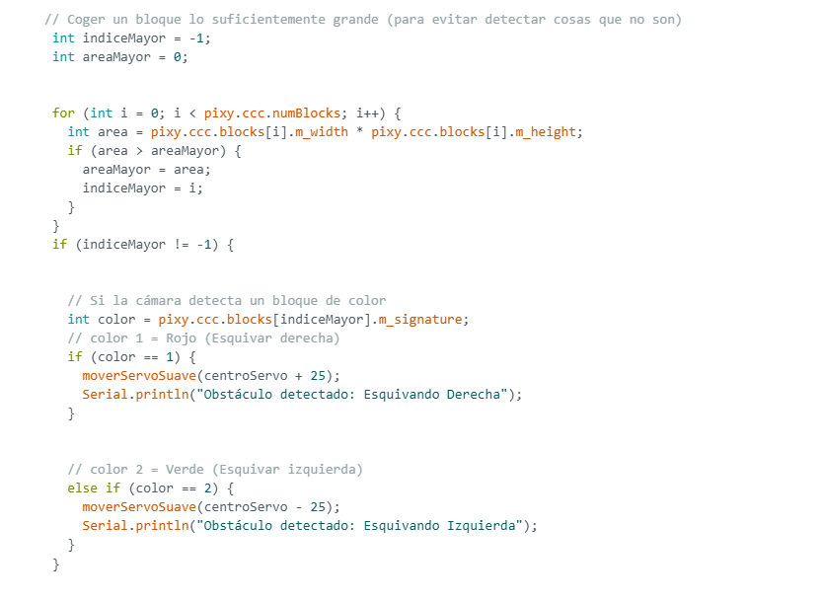
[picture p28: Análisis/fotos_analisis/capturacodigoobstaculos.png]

</p>

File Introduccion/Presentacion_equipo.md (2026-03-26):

# Presentacción del equipo
¡Hola! Somos Azzaiteras WALL-E, un equipo compuesto por Noa Torres Serra, Eva Espinosa Ortiz y Lidia Requena Torres. Somos dos actuales alumnas y una exalumna del IES Az-Zait, un pequeño instituto de Jaén con un gran equipo de robótica.
(foto del equipo)

## Sobre Eva
¡Hola! Soy Eva. Tengo 15 años y soy una estudiante del instituto Az-Zait. Estoy en 4º de ESO y desde que entré he estado en el equipo de robótica. He participado dos veces en dos años diferentes en la WRO de Jaén, he estado en la WRO Nacional en 2023 en la Seu d´Urgel. También he participado en la WRO de Madrid. Y en la última competición en la que participé fue en el Open de Brescia, en septiembre de 2024. Soy una chica trabajadora, graciosa y a veces demasiado perfeccionista. Por eso mismo, me gusta desconectar y disfrutar con mis amigos los fin de semana. 
<p align="center">

</p>

## Sobre Lidia
Mi nombre es Lidia Requena Torres, tengo 16 años y actualmente estoy estudiando en otro instituto un grado formativo sobre Atención a Personas en Situación de Dependencia. Llevo los cuatro años de la ESO participando en robótica, ya que me parece muy interesante, entretenido y lo más importante, ¡divertido! Me dieron la oportunidad de seguir participando por las tardes y no me lo pensé. Aprendo mucho con nuestro maravilloso profesor y me lo paso genial con mi equipo. Mis hobbies son jugar al fútbol, estar con mis amigos y familia. Me gustan mucho estar con los niños pequeños.
(foto Lidia)

## Sobre Noa
Hola, mi nombre es Noa Torres Serra, tengo 15 años y soy alumna del instituto IES Az-zait de Jaén. Actualmente estoy estudiando 4º de la ESO y llevo los cuatro años partcipando en el taller de robótica. He participado en dos competiciones nacionales: Almería 2024 y Cáceres 2025. También tuve la oportunidad de asistir a la nacional en la Seu d´Urgel. Estas experiancias me han enseñado mucho y he pasado muy buenos momentos en ellas, por eso mismo,¡voy a repetir este año!. Me considero una persona súper activa, me encanta participar en cualquier actividad que me permita aprender, viajar o conocer gente.
<p align="center">
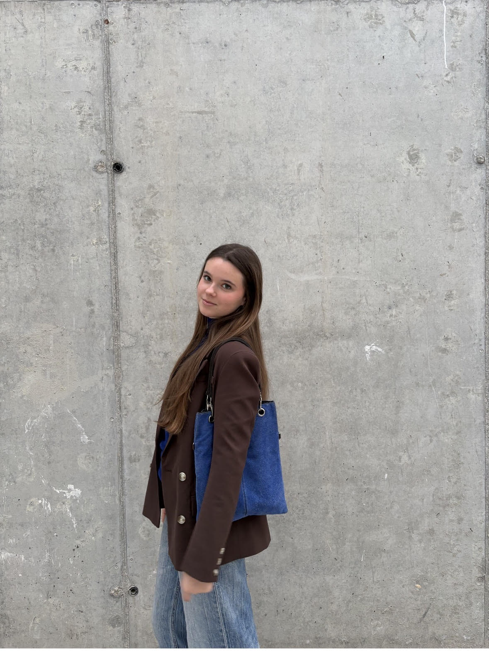
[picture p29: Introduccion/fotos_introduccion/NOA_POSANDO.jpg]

</p>

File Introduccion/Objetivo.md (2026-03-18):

# Objetivo del reto
El objetivo de este reto es que nuestro coche autónomo sea capaz de conducir de manera totalmente autónoma adaptándose a un circuito cuya dirección cambia de forma aleatoria en cada ronda, lo que implica que el vehículo debe ajustarse rápidamente a nuevas condiciones, todo sin intervención humana, asegurando así una conducción eficiente y segura en cualquier escenario que se le presente.

<p align="center">
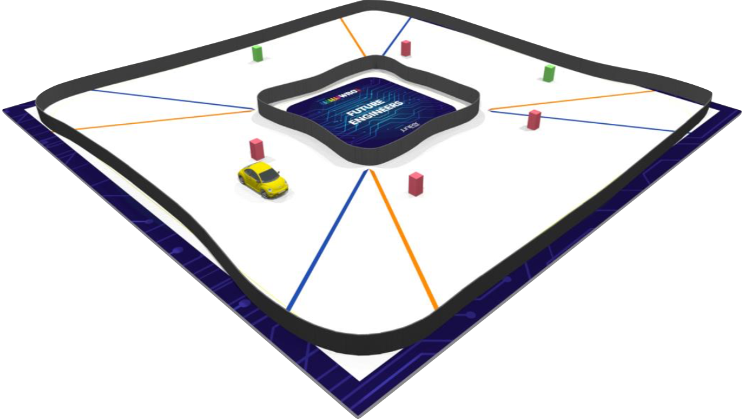
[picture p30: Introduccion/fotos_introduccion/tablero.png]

</p>

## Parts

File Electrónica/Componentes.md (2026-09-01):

# Componentes del robot

| Componentes |  Modelo |
| :--- | :---: |
| Servomotor| MG996R |
| Escudo | L298N |
| Sensores de ultrasonidos|  HC-SR04  |
| Placa | Arduino Uno |
| Motor| Modelo TT con reducción de velocidad 1:40. |
| Baterías | 2 x 18650 of 9900 mAh cada una |
| Cámara |PixyCam 2 |

## Servomotor
Basándonos en experiencias anteriores, directamente hemos optado por el servomotor MG996R ya que funciona controlando ángulos de giro en lugar de controlar la velocidad del propio servomotor. Esto facilita bastante todo ya que ahora podemos mover las ruedas delanteras con más precisión y requiriendo mucho menos esfuerzo. El modelo que elegimos fue el MG996R, como ya he dicho, ya que es conocido por ser más potente y por tener un buen rango de movimiento para este tipo de proyectos.

|  | **Specifications** |
|---|---|
| **Model:** MG996R | **Operating Voltage:** 4.8V – 7.2V |
| **Logic Voltage:** 3.3V / 5V compatible | **PWM Frequency:** 50 Hz (20 ms period) |
| **Stall Torque:** 9.4 kg·cm @ 4.8V / 11 kg·cm @ 6.0V | **Features:** Digital servo, metal gears, dual ball bearings, approximately 180° rotation|
| **Control Interface:** PWM (3-wire: Signal, VCC, GND) | **Operating speed:** 0.17 s/60° @ 4.8V, 0.14 s/60° @ 6.0V |
| 🔗 **[Buy Here](https://www.lcsc.com/product-image/C112633.html)** | **Function:** Controls the steering system |

<p align="center">
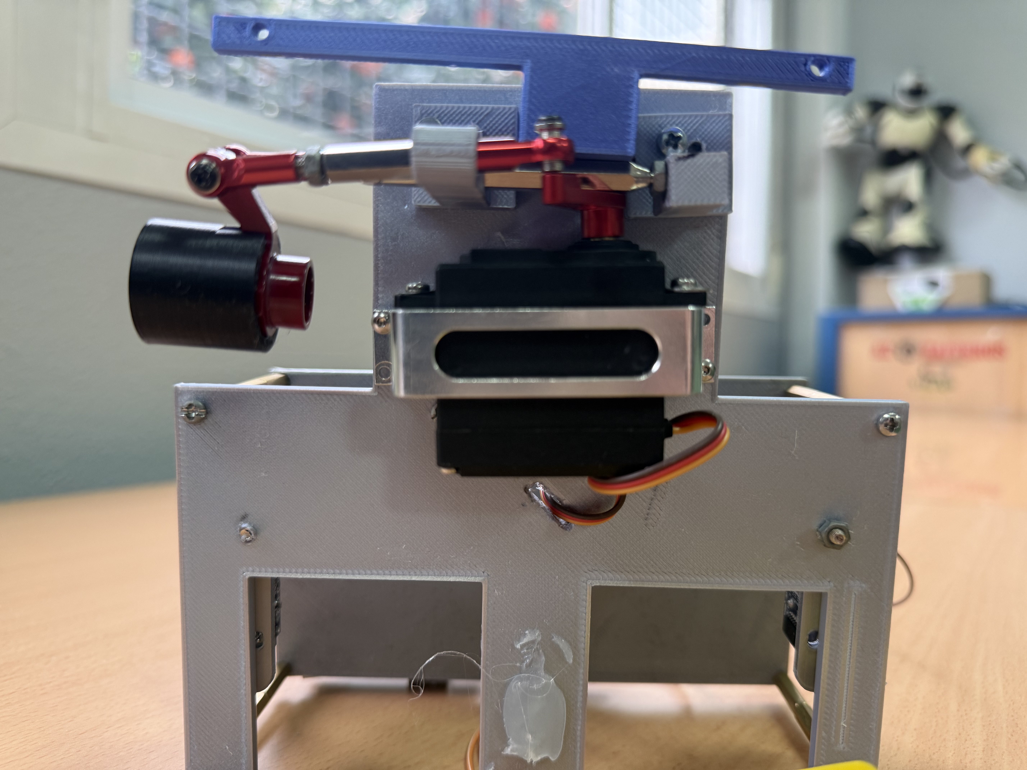
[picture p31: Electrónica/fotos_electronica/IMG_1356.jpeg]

</p>

## Escudo
El escudo que hemos utilizado ha sido el modelo L298N, y lo usamos principalmente para hacer las conexiones de los motores. Este escudo nos ha permitido controlar el movimiento de los motores de una forma más sencilla, ya que se encarga de enviar la energía necesaria para que funcionen correctamente. Además ya eramos conscientes de la incompatibilidad del escudo DRV8835 de Pololu con nuestros motores. Por lo tanto, seleccionamos directamente el modelo L298N.

|  | **Specifications** |
|---|---|
| **Model:** L298N Dual H-Bridge Motor Driver Module | **Operating Voltage:** 5V – 35V (motor supply) |
| **Logic Voltage:** 5V TTL compatible | **PWM Frequency:** Up to 25–30 kHz |
| **Max Continuous Current:** 2A per channel  |**Max Peak Current:** 3A per channel (short duration)|
| **Control Interface:** PWM + Direction pins (IN1–IN4, ENA, ENB) |**Built-in Features:** Dual H-Bridge, 5V regulator (78M05), thermal protection, flyback diodes |
| 🔗 **[Buy Here](https://www.lcsc.com/product-image/C112633.html)** | **Function:** Controls the speed and direction of DC motors and stepper motors using PWM and H-Bridge switching |

<p align="center">
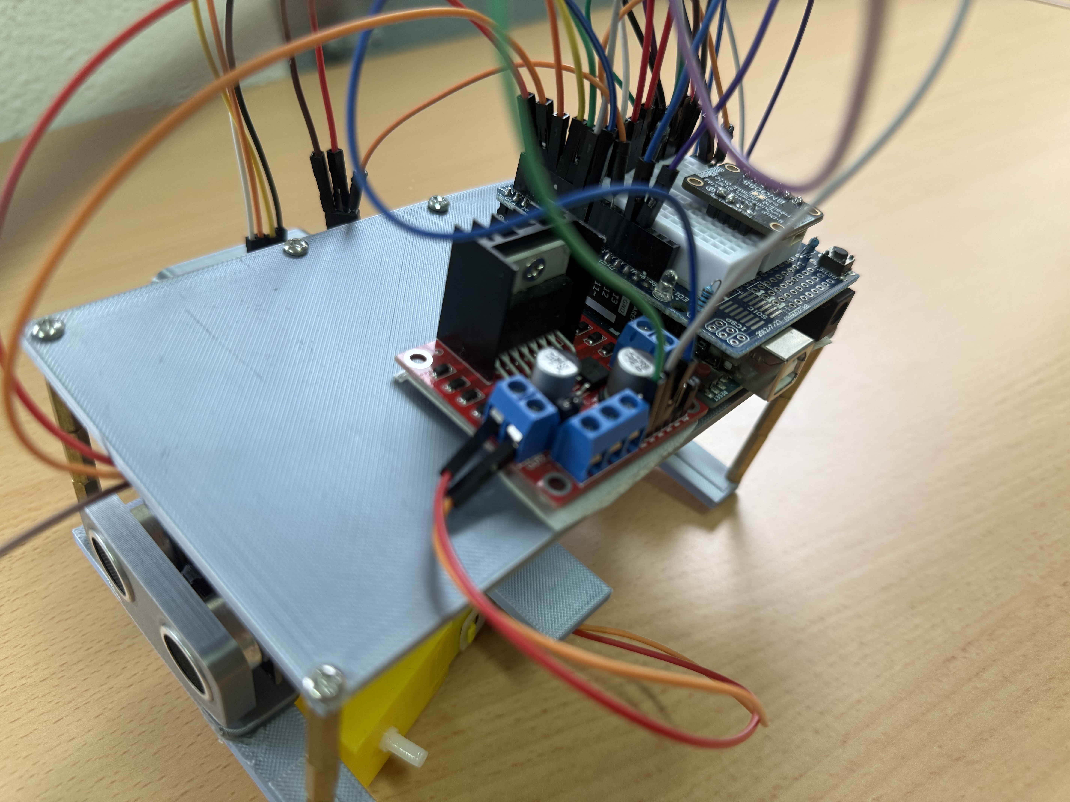
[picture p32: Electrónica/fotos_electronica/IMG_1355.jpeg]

</p>

## Sensores de ultrasonidos 
Para la correcta programación de nuestro robot necesitábamos disponer de tres sensores ultrasónicos de distancia para conseguir que el robot no impactara ni tocara ninguna pared. Para la implementación de estos en el chasis utilizamos una estructura diseñada previamente en la interfaz de TinkerCad y la imprimimos en 3D. Esto nos permitió sujetar bien los tres sensores de ultrasonidos. De tal modo que nos aseguramos que los sensores se mantienen en su sitio sin caerse mientras hacíamos pruebas.

|  | **Specifications** |
|---|---|
| **Model:** HC-SRO4 | **Operating Voltage:** 5V DC |
| **Logic Voltage:** 5V TTL compatible | **PWM Frequency:** 40 kHz |
| **Measuring Range:** 2 cm – 400 cm |**Measurement Accuracy:** ±3 mm|
| **Control Interface:** Trigger (TRIG) + Echo (ECHO) digital pins |**Built-in Features:** Non-contact distance measurement, low power consumption, automatic echo detection |
| 🔗 **[Buy Here](https://www.lcsc.com/product-image/C112633.html)** | **Function:** Measures the distance to objects by transmitting and receiving ultrasonic waves|

<p align="center">
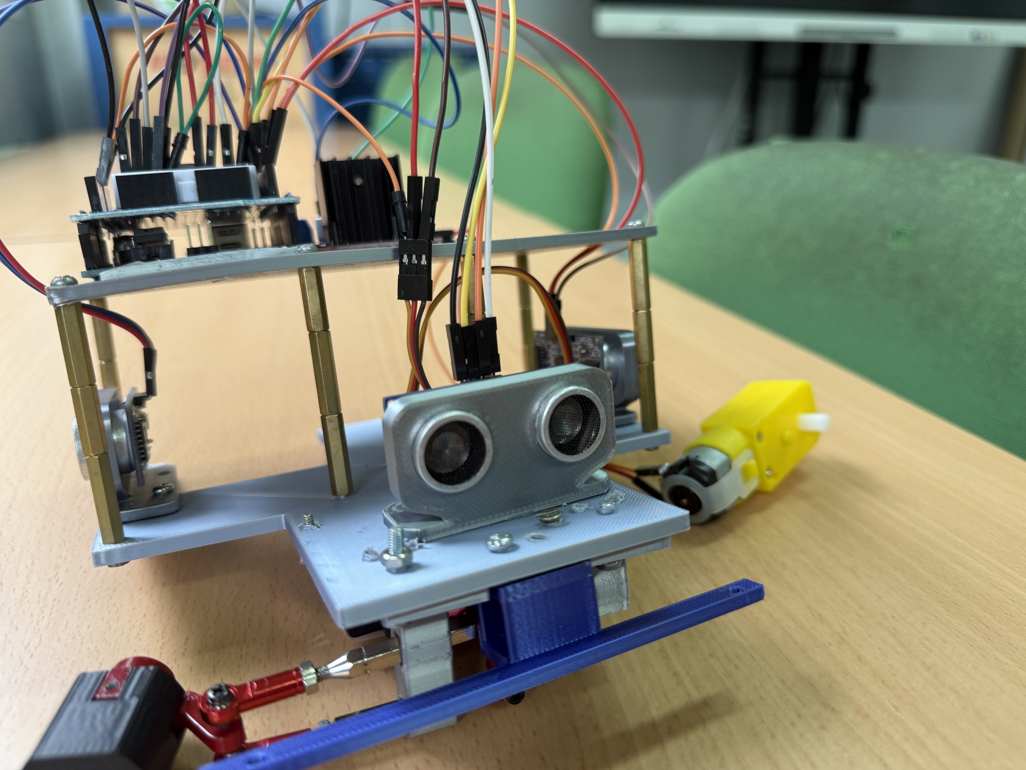
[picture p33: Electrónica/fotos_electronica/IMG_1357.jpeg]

</p>

## Placa 
La placa que hemos utilizado para nuestro robot ha sido la Arduino Uno R3. Decidimos usar esta placa porque ya habíamos trabajado con Arduino en otras ocasiones y nos parecía más fácil de entender. Además, es muy útil para conectar sensores, cables y otros componentes debido a su multitud de pines, y luego programarla para que funcione como queremos. Gracias a esto, pudimos hacer la programación del robot de forma más sencilla y aprender mejor cómo funciona la programación y la electrónica.

|  | **Specifications** |
|---|---|
| **Model:** Arduino Uno R3 | **Operating Voltage:** 5V  |
| **Input Voltage:** 7–12V recommended (6–20V limit) | **Clock Frequency:** 16 MHz |
|**Microcontroller:** ATmega328P|**Memory:** 32 KB Flash, 2 KB SRAM, 1 KB EEPROM|
| **Digital I/O Pins:** 14 (6 PWM outputs) |**Analog Inputs:** 6 (10-bit ADC) |
| **Communication Interfaces:** UART, I²C, SPI, USB|**Features:** USB Type-B, ICSP header, reset button, onboard voltage regulator, replaceable ATmega328P |
| 🔗 **[Buy Here](https://www.lcsc.com/product-image/C112633.html)** | **Function:** Programmable microcontroller board for controlling sensors, actuators, and embedded electronic systems. |

<p align="center">
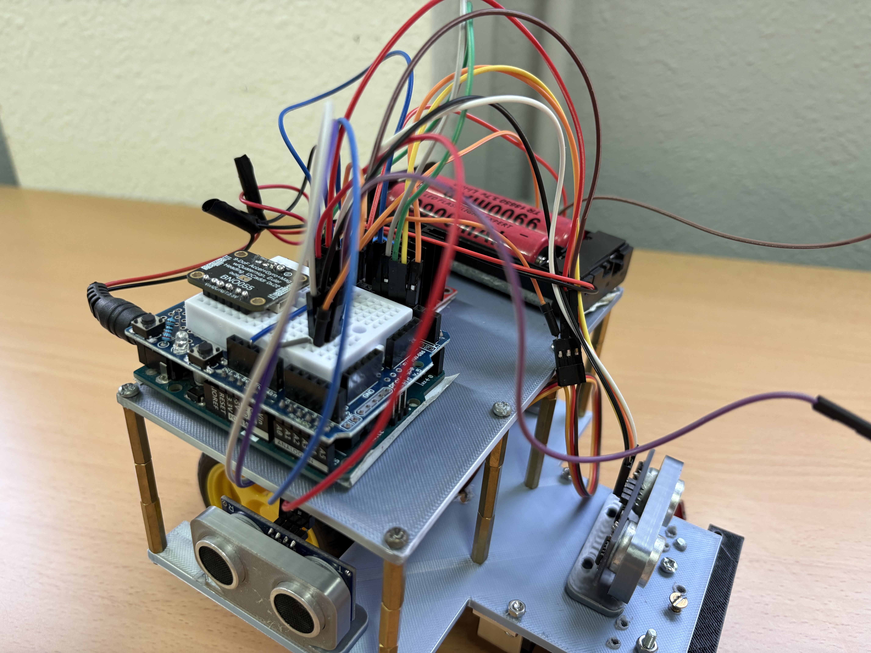
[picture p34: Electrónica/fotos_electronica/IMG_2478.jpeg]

</p>

## Motor
Para conseguir que el robot se pueda mover, hemos utilizado solo un motor que van conectados a las ruedas traseras. No pusimos motores en las ruedas delanteras porque no eran necesarios. En vez de eso, decidimos controlar la dirección del robot usando dos ruedas delanteras que están conectadas a un servomotor. De tal manera que el servomotor permite que el robot se mueva hacia la izquierda o hacia la derecha, encargándose de su dirección.

|  | **Specifications** |
|---|---|
| **Model:** TT DC Gear Motor| **Operating Voltage:** 3V – 6V DC  |
|**Rated Voltage:** 6V DC | **No-Load Speed:** ≈200 RPM @ 6V (varies by gear ratio) |
|**Stall Current:** ≈1.2 A|**No-Load Current:** ≈150–250 mA|
|**Output Shaft:** Double D Shaft |**Gearbox Type:** Plastic reduction gearbox|
|**Motor Type:** Brushed DC Motor|**Features:** High torque, low cost, lightweight, suitable for robot cars |
| 🔗 **[Buy Here](https://www.lcsc.com/product-image/C112633.html)** | **Function:** Provides rotational motion to drive robot wheels and other small mechanical systems. |

<p align="center">
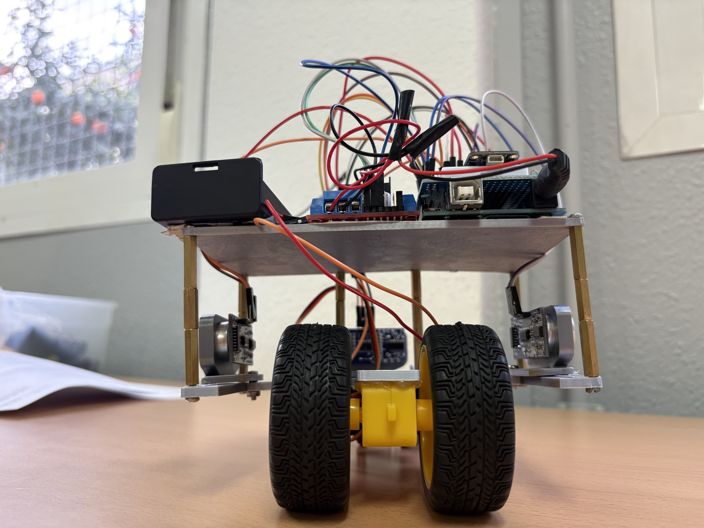
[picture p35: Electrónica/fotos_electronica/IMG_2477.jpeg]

</p>

## Baterías
Las baterías 18650 que son de ion de litio son ampliamente usadas en robótica y electrónica, y es por esto que son las que hemos usado. Su voltaje máximo son 4.2 V cargadas completamente. Y la capacidad de la batería en este caso, 9900 mAh (aunque muchas veces las baterías baratas "de 9900 mAh" no entregan realmente esa capacidad; suelen estar sobreestimadas). Con las dos baterías apiladas en serie tendríamos para 4 cargas enteras de un móvil, por ejemplo. Además, un beneficio de estas baterías es que son recargables. 

|  | **Specifications** |
|---|---|
| **Model:** 18650 Li-ion Rechargeable Battery| **Nominal Voltage:** 3.7V |
|**Maximum Voltage:** 4.2V (fully charged) | **Minimum Discharge Voltage:** 2.5–3.0V |
|**Rated Capacity:** 9900 mAh*|**Rechargeable:** Yes|
|**Configuration:** Can be connected in series or parallel |**Battery Type:** Lithium-ion (Li-ion)|
|**Note:** Many low-cost batteries advertised as 9900 mAh do not actually achieve this capacity. Most genuine 18650 Li-ion cells from reputable manufacturers have capacities in the 2000–3500 mAh range|**Features:** High energy density, low self-discharge, rechargeable, lightweight |
| 🔗 **[Buy Here](https://www.lcsc.com/product-image/C112633.html)** | **Function:** Supplies portable power for robotics, electronic projects, and battery-powered systems. |

<p align="center">

</p>

## Cámara

|  | **Specifications** |
|---|---|
| **Model:** Pixy2 CMUcam5| **Nominal Voltage:** 5V DC (regulated) or 6–10V DC (unregulated, via Vin pin) |
|**Logic Voltage:** 3.3V (digital/I2C lines) |  **Current Consumption:** ~140 mA at 5V|
|**Image Sensor:** Aptina MT9M114, 1296×976 resolution with integrated image flow processor |**Field of View:** 60° horizontal, 40° vertical|
|**Frame Rate:** 60 fps (16.7 ms per frame) | **Processor:** NXP LPC4330, dual-core, 204 MHz|
|**Control Interface:** UART serial, SPI, I2C, USB, digital, analog|**Built-in Features:** Color-based object learning/detection, line and intersection tracking, barcode-style "road sign" detection, onboard memory for up to 7 saved objects, integrated LED light source (~20 lumens)|
| 🔗 **[Buy Here](https://www.lcsc.com/product-image/C112633.html)** |**Function:** Smart vision sensor that processes images onboard to recognize and track objects by color, lines, and signs — freeing the main microcontroller (Arduino/Raspberry Pi) from that processing load. |

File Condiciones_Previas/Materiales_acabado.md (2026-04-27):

# Listado de componentes y materiales
- Chasis: impresión 3D y pasadores: permiten la colocación de todos los componentes con suficiente espacio para que el mecanismo de dirección delantero no interfiera con el resto.
- Placa Arduino Uno: controla todos los componentes del robot, como los motores, el servomotor y los sensores. Estos se conectan a la placa Arduino.
- Servomotor MG996R: principal responsable del mecanismo de dirección delantero. Se controla mediante una librería de servos en el IDE de Arduino.
- Motor modelo TT con reducción de velocidad 1:40 que proporciona el movimiento del robot. Se conecta al escudo del motor L298N.
- Ruedas con un diámetro de [cm]: conectadas a los motores traseros para su control.
- Tres sensores ultrasónicos HC-SR04 para medir distancias: deben medir y calcular la distancia entre las paredes y los obstáculos.
- Cableado electrónico: placa de prototipos, cables puente macho-macho, cables puente hembra-macho y controlador de motor L298N. Permite la comunicación entre la placa Arduino y el resto de los componentes.
- Fuente de alimentación: dos baterías 18650 de 3,7 V y 9900 mAh conectadas en serie en su portapilas, que proporcionan la energía suficiente para el correcto funcionamiento del robot.
- Giroscopio BNO055: permite al robot realizar giros con mayor precisión, ajustándose a ángulos específicos mediante programación. Controlado también por una librería de giroscopios en el IDE de Arduino.
- Mecanismo de las ruedas delanteras: fabricado con piezas impresas en 3D que sujetan el mecanismo para que el robot pueda girar correctamente.

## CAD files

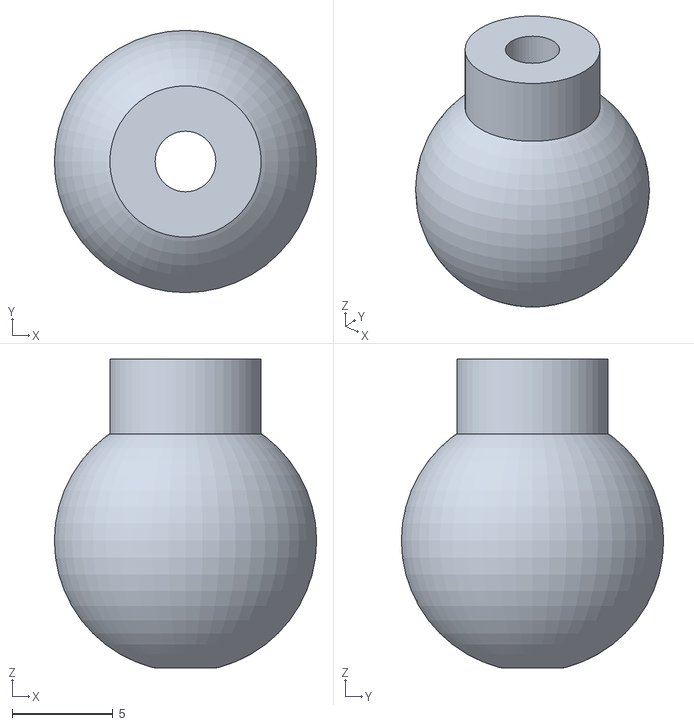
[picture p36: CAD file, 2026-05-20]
Archivos_en3D/Pieza imposible (13).stl
13.0 x 13.0 x 15.3

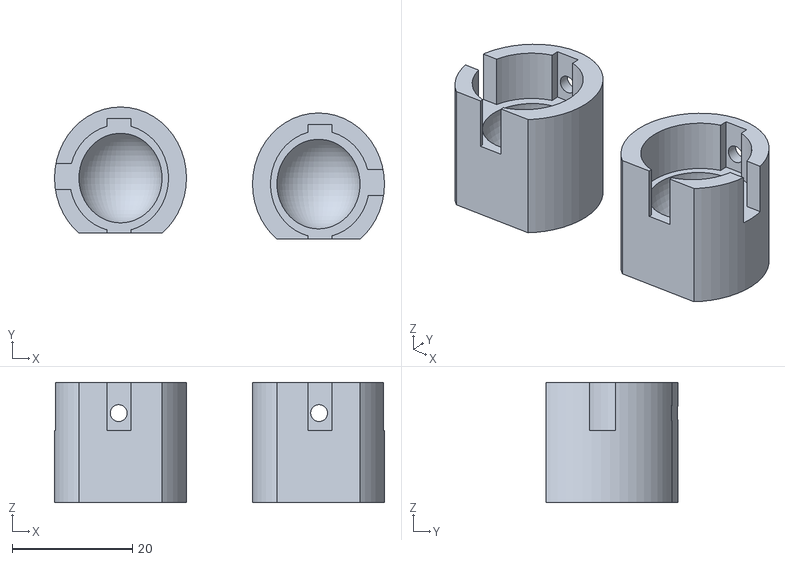
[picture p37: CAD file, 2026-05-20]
Archivos_en3D/Pieza imposible (12).stl
55.0 x 22.0 x 20.0

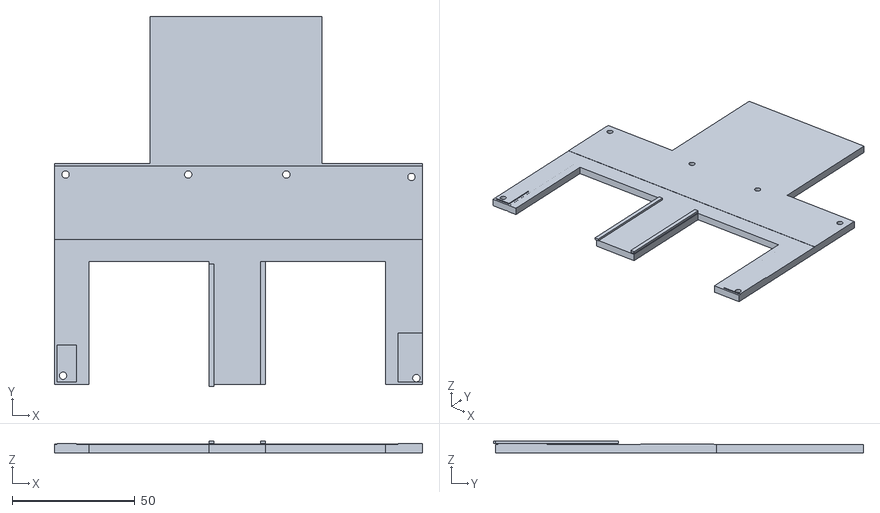
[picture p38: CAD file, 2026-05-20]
Archivos_en3D/CHASIS.stl
150.0 x 151.0 x 5.00

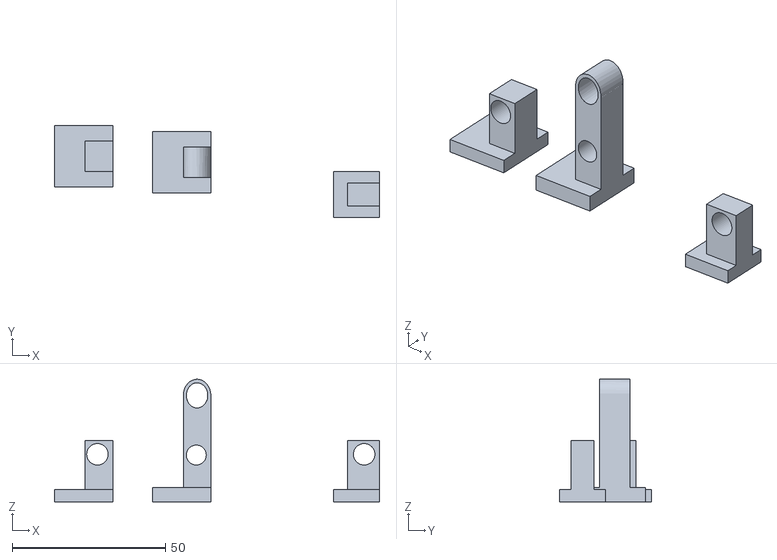
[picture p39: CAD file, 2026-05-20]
Archivos_en3D/PIEZA SUJETA DOS BARRAS - EVA.stl
106.0 x 30.0 x 40.0

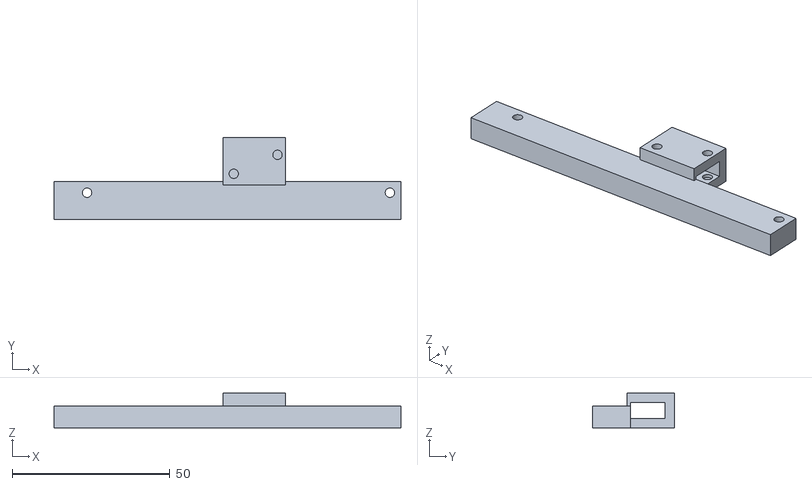
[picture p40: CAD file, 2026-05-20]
Archivos_en3D/Mecanismo ruedas delanteras con dos agujeros.stl
110.0 x 26.0 x 11.0

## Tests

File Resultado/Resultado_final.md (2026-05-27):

<h1 align="center">Resultado final </h1>
Después de todo el trabajo realizado y de la incorporación de todos los componentes en la programación, este es el resultado final de nuestro robot "**WALL-E**". 

| **Vídeos Finales**                       |
| :--------------------------------------------------- |
| Los vídeos de rendimiento deben demostrar el desempeño del vehículo de principio a fin en cada desafío. Pueden incluir comentarios, títulos o animaciones. Asimismo, pueden abarcar aspectos de las secciones 1, 2 o 3. |
| [Videos de demostración](https://www.youtube.com/watch?v=cXj32blsBB0)  |
| [Canal de youtube](https://youtube.com/@evaespinosaortiz4305?si=ZbZFucF2qKW5FEGj)  | 

La próxima semana continuaremos enfocándonos en la programación del robot, con el objetivo de perfeccionar su funcionamiento e implementar la cámara PixyCam para la realización de la segunda prueba: Obstacle Challenge.

| ** Fotos – Vehículo y Equipo **    |
| :------------------------------------------------------------------------------------------------------------------------------------------------------------------------------------------------------------------------------------------------------------------------------------------------------------------------------------------------------------------------------------------------------------------- |
|Se deben proporcionar fotografías del equipo y del robot. Las fotografías del robot deben abarcar todos sus lados, ser nítidas, estar enfocadas y mostrar aspectos de su movilidad, potencia, sensibilidad y capacidad para superar obstáculos. Se puede hacer referencia a estas fotografías en las secciones 1, 2 y 3 del análisis. Es necesaria una foto del equipo para que los jueces puedan identificarlo durante las competiciones locales e internacionales. |
| [Fotos del vehículo](Fotos_robot/ArchivodeFotos.md)  |
| [Fotos del equipo](Fotos_equipo/)  |     

<table>
  <tr>
    <td>
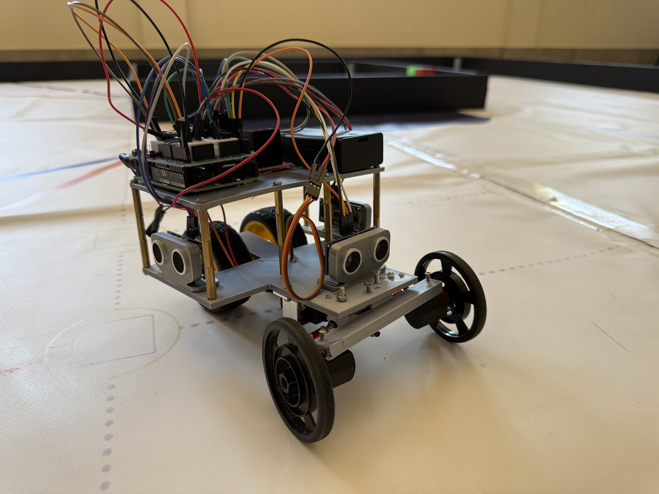
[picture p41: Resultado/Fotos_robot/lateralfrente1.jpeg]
Top View
      
      <p style="text-align: center; font-size: 24px; font-weight: bold;">WALL-E</p>
    </td>
  </tr>
</table>

(https://www.youtube.com/watch?v=cXj32blsBB0)

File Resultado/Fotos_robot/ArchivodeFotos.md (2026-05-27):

<table>
  <tr>
    <td>
      Top View
      <p style="text-align: center; font-size: 24px; font-weight: bold;">WALL-E</p>
    </td>
  </tr>
</table>

<table>
  <tr>
    <td>
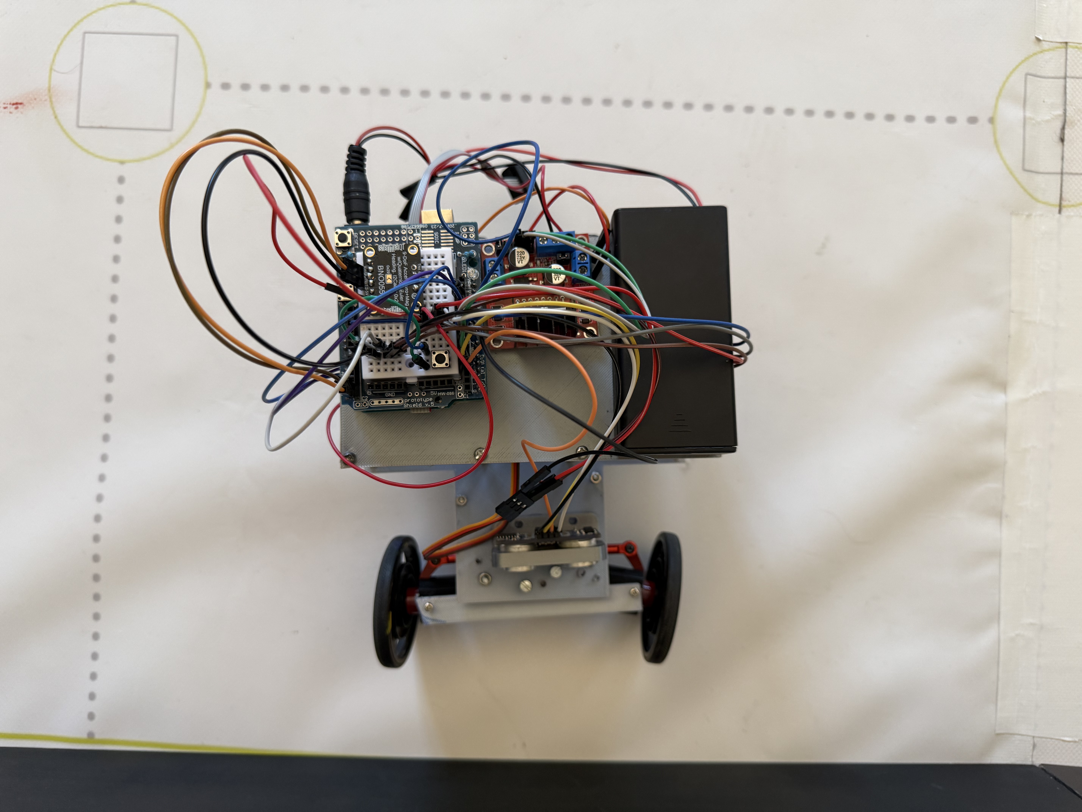
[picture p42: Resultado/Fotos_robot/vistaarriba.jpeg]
      
      <p style="text-align: center; font-size: 24px; font-weight: bold;">Top View</p>
    </td>
    <td>
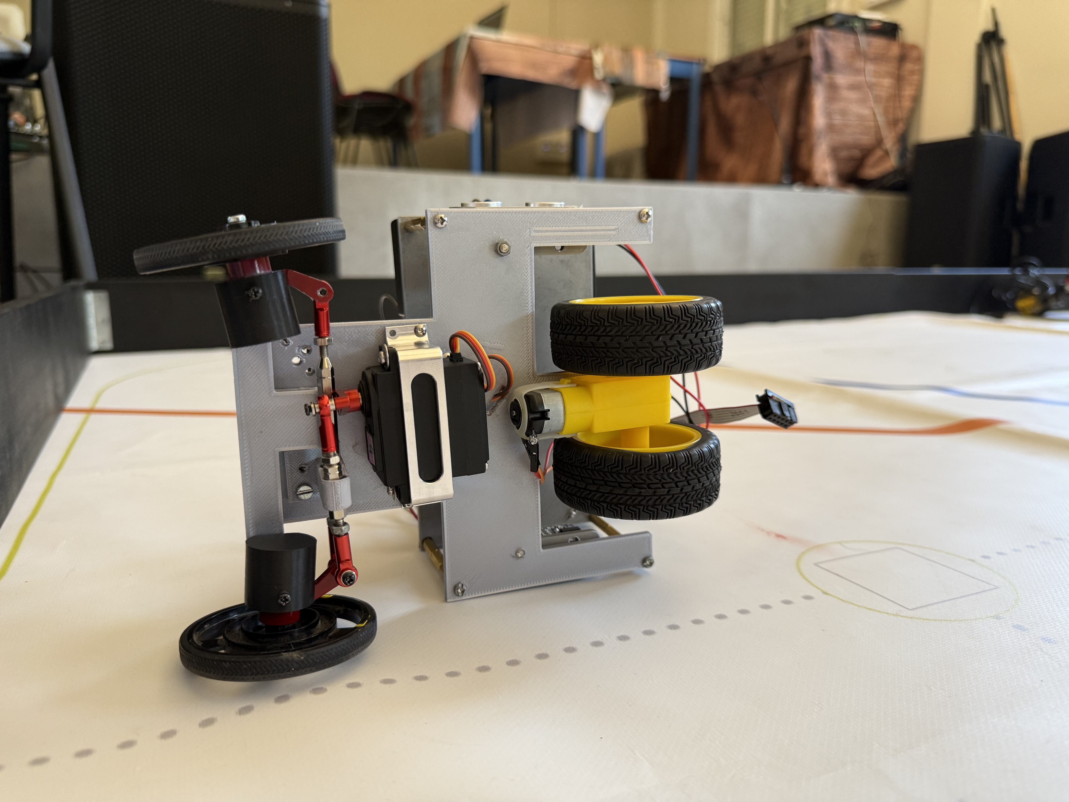
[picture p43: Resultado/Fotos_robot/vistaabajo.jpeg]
Bottom View
      
      <p style="text-align: center; font-size: 24px; font-weight: bold;">Bottom View</p>
    </td>
  </tr>
  <tr>
    <td>
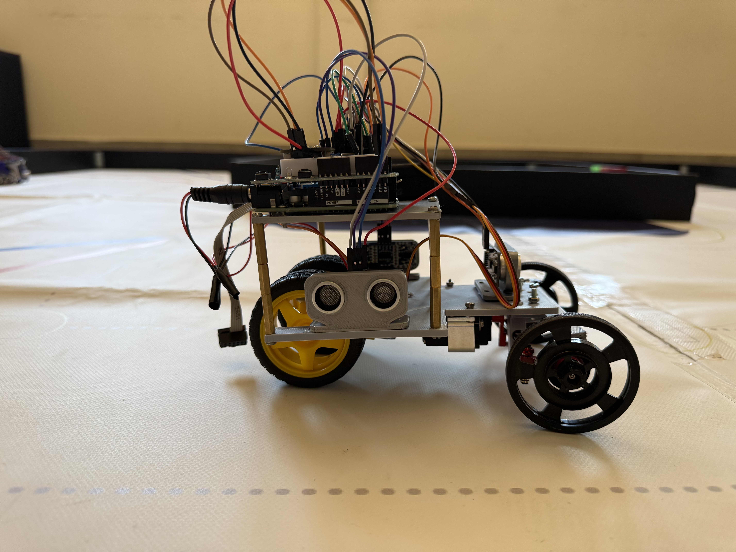
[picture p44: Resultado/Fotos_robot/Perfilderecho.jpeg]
Right View
      
      <p style="text-align: center; font-size: 24px; font-weight: bold;">Right View</p>
    </td>
    <td>
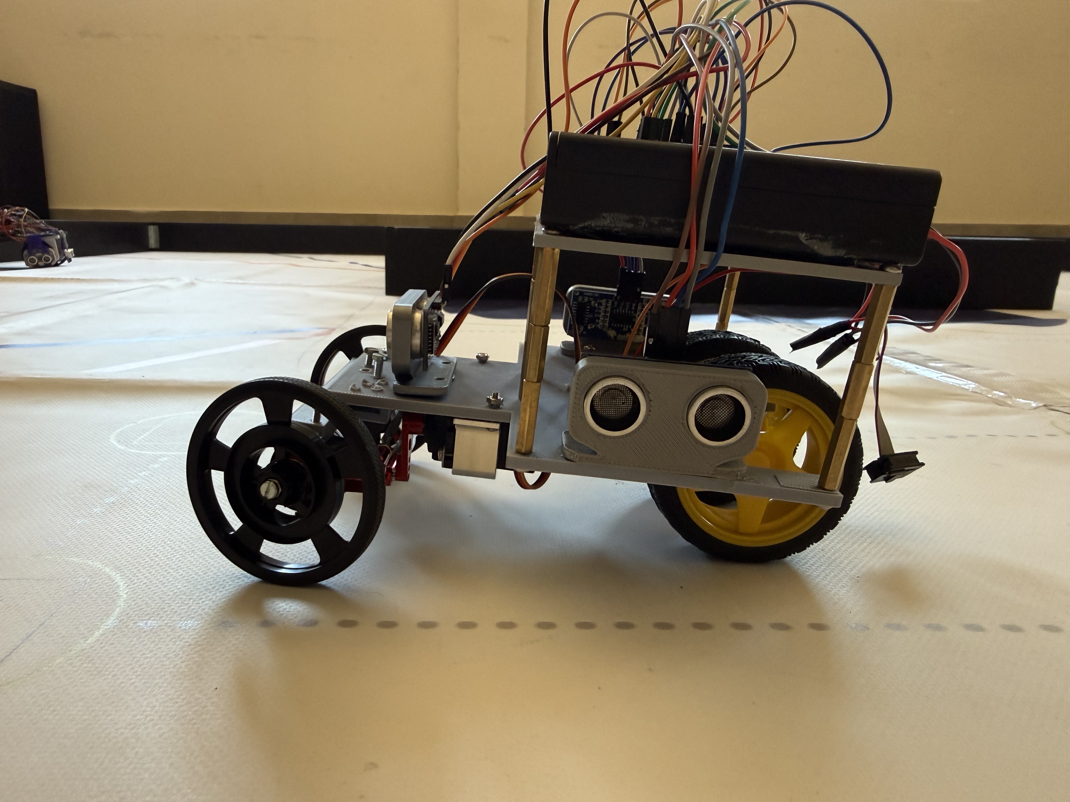
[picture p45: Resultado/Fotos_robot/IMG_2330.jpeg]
Left View
      
      <p style="text-align: center; font-size: 24px; font-weight: bold;">Left View</p>
    </td>
  </tr>
  <tr>
    <td>
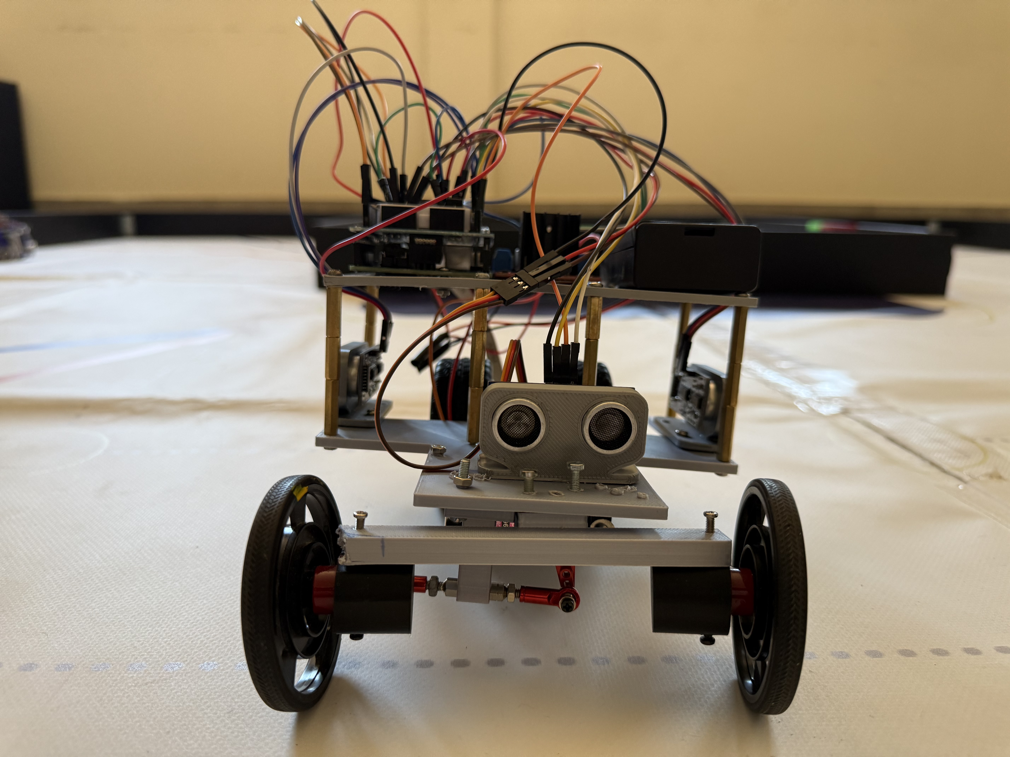
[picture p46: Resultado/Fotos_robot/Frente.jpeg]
Back View
      
      <p style="text-align: center; font-size: 24px; font-weight: bold;">Face View</p>
    </td>
    <td>
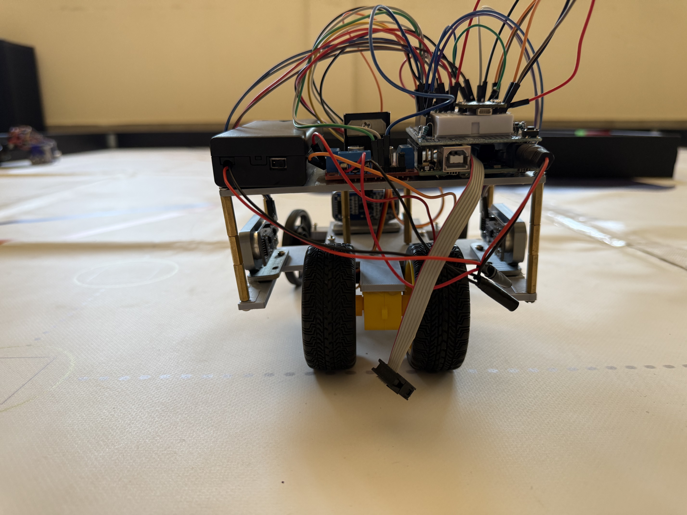
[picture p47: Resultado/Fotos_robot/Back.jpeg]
Front View
      
      <p style="text-align: center; font-size: 24px; font-weight: bold;">Rear View</p>
    </td>
  </tr>
</table>

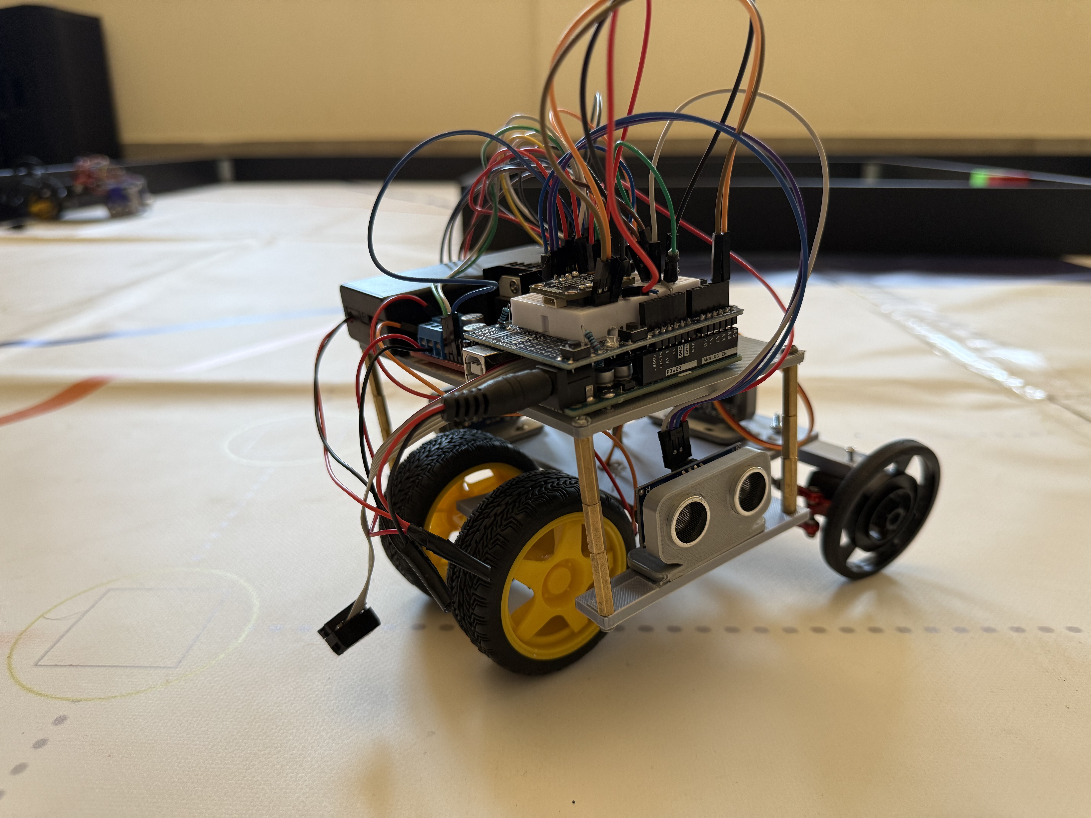
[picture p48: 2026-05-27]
Resultado/Fotos_robot/lateralback2.jpeg

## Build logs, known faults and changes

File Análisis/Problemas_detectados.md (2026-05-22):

# Problemas detectados
Durante el desarrollo del robot, que funciona de forma parecida a un coche autónomo, nos encontramos con bastantes problemas que tuvimos que ir solucionando poco a poco. Uno de los primeros fallos que vimos fue que, cuando el robot avanzaba rápido, la parte delantera se levantaba haciendo “caballito”. Esto hacía que perdiera estabilidad y que el movimiento no fuera seguro ni preciso.
Después de varias pruebas, decidimos colocar un contrapeso en la parte delantera para repartir mejor el peso. Gracias a eso, el robot consiguió mantenerse más equilibrado y avanzar de una manera mucho más estable, son levantarse la parte delantera.
Otra de las partes que más trabajo nos dio fue el mecanismo de dirección. Para montarlo, necesitábamos una pieza hecha con impresión 3D, pero desde el principio tuvimos muchos problemas porque las primeras versiones no encajaban bien y la dirección no funcionaba correctamente. Tuvimos que modificar la pieza varias veces, cambiando medidas y reforzando algunas zonas hasta conseguir que quedara bien colocada. Cada vez que hacíamos un cambio teníamos que volver a imprimirla y probarla otra vez, así que fue un proceso largo, pero al final conseguimos una pieza mucho más resistente y que permitía que la dirección funcionara mejor.

Además, la propia dirección también nos dio problemas durante las pruebas. A veces giraba con dificultad y otras veces los tornillos se aflojaban con el movimiento y las vibraciones del robot. Y otras veces, realizaba un pequeño sonido el servomotor sin hacer nada más. Para solucionarlo, revisamos todas las uniones, ajustamos mejor los tornillos y reforzamos algunas partes para que el sistema quedara más firme y estable.
También tuvimos dificultades con una de las ruedas. Había que apretarla en el punto exacto porque, si estaba demasiado floja, podía salirse, pero si la apretábamos demasiado, la rueda no giraba bien y el robot se movía mal ya que derrapaba al no funcionar una de las ruedas. Después de hacer varias pruebas, conseguimos encontrar el ajuste adecuado para que la rueda se mantuviera fija y pudiera girar correctamente sin que se cayera todo el rato.

La programación fue otra de las partes más complicadas. Como el robot tenía un mecanismo de dirección y además utilizaba un giroscopio, al principio no sabíamos muy bien cómo programarlo para que se moviera correctamente. Por eso tuvimos que empezar prácticamente desde cero, buscando información, viendo ejemplos y haciendo pequeñas pruebas para entender cómo funcionaban los sensores y cómo podíamos controlar los movimientos del robot. Poco a poco fuimos corrigiendo errores y mejorando el programa hasta conseguir que respondiera de una forma más precisa y estable. Todo esto lo conseguimos haciendo pequeñas pruebas, hasta juntarlo todo.
Por último, cuando empezamos a hacer las pruebas finales, nos dimos cuenta de que el tapete también nos daba problemas. Había estado guardado doblado y tenía muchas arrugas, por lo que la superficie no era completamente lisa. Esto hacía que el robot a veces no avanzara recto, se desviara o girara más de lo que debía, provocando que no completara bien las vueltas programadas. Para intentar solucionarlo, tratamos de alisar el tapete y repetimos las pruebas varias veces, ajustando también algunos parámetros del programa para reducir esos errores.

Las  pilas son de pocos voltios, por lo que las hemos puesto de más voltios y cargadas para que vaya el robot más rápido y sean los giros más precisos y con el giroscopio realice bien las tres vueltas sin pasarse o quedarse corto.

## Motor y estructura:
- Unas de las piezas para sujetar el motor no encajaba correctamente, ya que no caímos en la colocación de las ruedas en el motor y la anchura de ellas, por lo que no podíamos meter el motor con el soporte impreso.
- La primera estructura/motor la realizamos de tres niveles, pero lo tuvimos que cambiar, y hacerlo de dos, ya que chocaba los componentes como la placa.
- En la parte  de abajo, se nos olvidó realizar el diseño con un agujero, para meter los cables, por lo que lo hicimos provisional casero.

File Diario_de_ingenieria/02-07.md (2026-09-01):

Hoy hemos avanzado con la documentación debido a que la impresora 3D necesitaba reparación y no podíamos volver a montar el sistema de dirección ya que necesitábamos las piezas nuevas ya arregladas. Por lo que dejamos la mecánica a un lado y aprovechamos el tiempo mejorando la documentación. Implementamos la creación de un logo y un nuevo apartado de la presentación del equipo en el archivo README.md

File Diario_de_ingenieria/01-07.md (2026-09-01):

Hoy ha sido nuestro primer día después de la competición regional. Hemos identificado todos los problemas anteriores que tuvimos y nos hemos enfocado principalmente en mejorar el mecanismo de dirección y en terminar de programar el obstacle challenge

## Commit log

2026-03-16 Agregar diseño del chasis y sus características
    Se describe el diseño del chasis, incluyendo la reducción de tamaño, la adición de un piso superior para componentes y ajustes para un solo motor trasero.
2026-03-16 Create listado de fotos.md
2026-03-18 Resize chassis image for better visibility
    Updated image size for the chassis diagram.
2026-03-18 Expand wiring instructions in Alimentacion.md
    Added detailed sections on wiring for L298N shield, ultrasonic sensors, and servomotor.
2026-03-18 Create para eliminar
2026-03-18 Add images and details for motor and sensor connections
2026-03-18 Add missing components to materiales_acabado.md
2026-04-17 Add description of steering mechanism
    Added a brief explanation of the steering mechanism.
2026-05-22 Add improvement proposals for robot obstacle detection
    Added proposals for future improvements to the robot, including obstacle detection using a camera and pending tasks for implementation.
